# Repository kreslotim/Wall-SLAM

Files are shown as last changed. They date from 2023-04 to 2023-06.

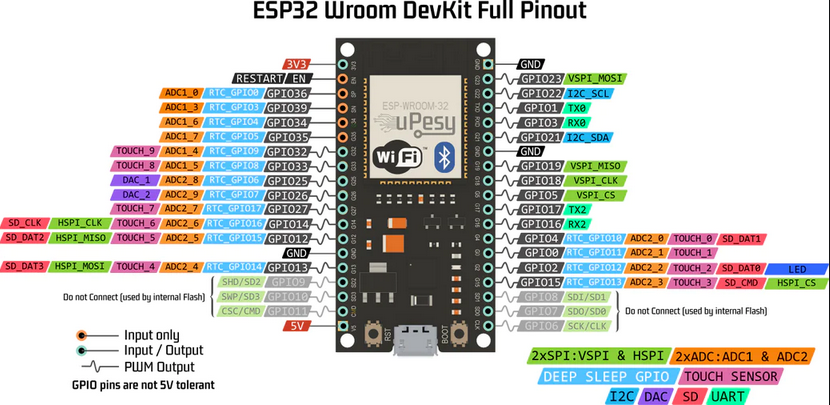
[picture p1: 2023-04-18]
circuit/ESP32-WROOM-38PINS.png

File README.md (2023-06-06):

# Wall-SLAM - Simultaneous Localization And Mapping

Timofey Kreslo, Sylvain Pichot, Finn MacNamara, Alonso Coaguila, Florian Dejean.



June 2023

## Description

Wall-SLAM is a project that we have developed within the course CS-358 Making Intelligent Things, under the direction of Prof. Koch and under the supervision of Federico Stella and Anirudhh Ramesh. This report outlines the key features, methodology, challenges faced, and a detailed “How To Build” guide.

Our [project proposal](https://github.com/kreslotim/Wall-SLAM/blob/main/proposal/proposal.md), can be useful to understand some deviations in our project from our expectations.

The primary objective of the project was to build a cost-effective and compact SLAM robot capable of mapping unknown and dynamic environments.

## Overview

https://github.com/kreslotim/Wall-SLAM/assets/56829239/a7d6daf9-7e9c-4008-a5e7-d5f0c00a2a69

Main idea:

We utilize the data from the distance sensors (Ultrasonic and LIDAR), IMU (Inertial Measurement Unit) sensor, and Stepper motors to estimate the robot's pose (position and orientation) and simultaneously construct a map of the environment. All this data will be processed and then displayed on a website. This involved integrating data from different sensors using techniques such as sensor calibration, fusion and Kalman filtering algorithms.

## Components and supplies

- ESP32
- NXP Precision 9DoF IMU
- VL53L1X Time of Flight Distance Sensor (2x)
- HC-SR04 Ultrasonic Sensor
- 180-Degree Servo
- Stepper motor 28byj-48 (2x)
- ULN2003 motor driver (2x)
- XL6009E1 DC-DC Voltage Converter - 5V
- 9V Battery supply
- Power Switch
- 3D Prints (STLs)

## 3D Design



As zealous devotees of the enchanting Disney’s figure Wall-E, we couldn’t resist the temptation to transform our prototype into his spitting image. But, alas, our professor promptly intervened, bursting our bubble of whimsy with a comic remark. He reminded us that while Wall-E excelled in garbage collection and exuded undeniable cuteness, our project’s aspirations extended beyond those realms. Thus, we bid farewell to our beloved Wall-E robot, sparing it from a destiny of cuteness overload and instead refocusing our efforts on more practical endeavors.

We decided to shift our focus to functionalities that would enable mapping of the surrounding environment, which is covered by SLAM. Additionally, we chose to retain the concept of tracks with wheels, as it offers enhanced precision in movement and rotation (especially the ability to turn on the spot), while opting for rubber tracks to minimize slippage during maneuvering. The adventure of building a SLAM robot starts here. Our first step is to build our robot, that we later named... Chewbacca, we will give a reason for that name at the end of the report. Meanwhile lets see how we built it. 

 <br/><br/>

### 1. Sketches



We started by sketching our ideas and figuring out how to arrange electronic components in the best way possible. Our main goal was to create a compact design that would make the assembly process easier and speed up 3D printing. This approach aimed to make the construction phase more efficient overall.

We initiated the development process by focusing on the chassis design. Subsequently, we proceeded to devise an arrangement strategy. The robot incorporated two stepper motors along with their corresponding drivers, a servo, a battery, and a micro-controller. For the initial prototype, we positioned both stepper motors at the rear section of the chassis. In order to counterbalance the weight distribution, the batteries and the micro-controller were placed at the front section. Lastly, the servo, responsible for holding the sensors, was centrally positioned within the chassis.



This approach was promptly dismissed as it became apparent that in order to facilitate turning, both motors needed to rotate in opposite directions, necessitating the rotation of the entire car around its vertical axis.

The rotation of the machine necessitates the alignment of the servo and the primary axis of rotation. This alignment is crucial during turning maneuvers as the distance sensors are required to scan in close proximity to the adjacent wall. By maintaining the sensors in close proximity to the central axis of rotation, the objective is to minimize noise and optimize the accuracy of the scanning process.

Consequently, we proposed an alternative design to address this limitation.

This design greatly appealed to us, and we made the decision to proceed in this particular direction. During our exploration on the web, we chanced upon a robot named [SMARS](https://www.smarsfan.com/) (Screwed/Screwless Modular assemblable Robotic System), which seemed to align closely with our envisioned requirements. We found inspiration in its design and opted to incorporate a chassis that closely resembled to SMARS. To assess the feasibility of the track concept, we even went as far as designing the entire SMARS idea to evaluate its effectiveness.

Having appreciated the remarkable ingenuity behind the notion of using the printing filament as a means to securely bind the tracks together, as well as the exceptional functionality of this approach in practical implementation, we wholeheartedly adopted this design for our project. Consequently, this decision entailed the utilization of the same wheels, as the tracks had been meticulously tailored to ensure precise compatibility with these specific wheel components. This deliberate alignment not only guaranteed optimal performance but also facilitated seamless integration between the tracks and wheels, thereby fortifying the overall effectiveness of our system.

The subsequent focus of our attention revolved around the development of the chassis, and the incorporation of the battery, the motors and the sensors.

As soon as we agreed on the placement of all the components, we started designing in 3D. In order to leverage the collaborative design features, we opted to use Fusion 360, allowing for effective teamwork during the design process. Minor design changes have been made in FreeCad, in order to save time.

Here’s what we’ve come up with.
<p align = "center">
 
 
</p>

Now we will explain the choice we’ve made for positioning the electronic pieces. The parts that are highlighted in green are those that we designed ourselves. The Ultrasonic sensor’s frame as well as the wheels and the tracks were borrowed from SMARS project, because they fit our requirements well.

<p align = "center">

</p>

While we adopted the wheel design from SMARS ([link for STLs](https://www.thingiverse.com/thing:2662828)), we had to adapt it’s axle mount to fit the rectangular axle of the motor we are using. Furthermore, it is essential to align the axle of the slave wheel with the motor’s axle to ensure that both wheels are at the same level.

<p align = "center">

</p>
 
In order to optimize the efficiency of the printing and assembly process, we strategically positioned all the components in close proximity to one another, ensuring minimal wasted space on the chassis.

As the heaviest electronic component of the entire construction, the battery serves as a central anchor within the overall design. By positioning it at the center, we establish a stable foundation upon which the remaining components, i.e. the servo and the sensors are securely mounted and connected.

<p align = "center">

</p>
 
The cover slides over the battery and encases the servo on top.

The servo, in return, holds both lidars (distance sensors) that are sneaked on the servo’s arm.
<p float = "left">


</p>
 
### 2. Assembly

Once the design was ready, it was printed at EPFL in DLL, and partly at home. Mostly PETG material was used, except for the tracks which were printed using FLEX rubber filament, under the consent of Sébastien Martinerie - 3D printing Coach at the SPOT. Caterpillars are connected by means of an ordinary filament in its initial form, as mentioned above.
<p align = "center">

</p>

To make power control easier, a switch has been added on top of the cover that holds the servo.
Given that multiple components, including the Arduino, operate at the same power level and share a common ground, the wires are soldered together in a centralized manner resembling the arrangement of an octopus




The opposite side of the switch features the motion sensor (IMU) securely attached to the cover that holds the servo, using screws:
<p align = "center">

</p>

<br/><br/>


Here the difficulty turned out to be to establish connections between numerous devices that rely on the I2C (Inter-Integrated Circuit) serial communication protocol. In particular, there was an issue with two lidars having the same address, preventing them from being connected on the same I2C bus. One possible solution would have been to use a multiplexer, but since one was not available, an alternative approach was devised through code.

<br/><br/>

To overcome this challenge, some of the ESP32 GPIOs needed to be reconfigured to function as I2C pins, to which we connected the front lidar. Subsequently, the motion sensor was connected to the standard I2C pins, and the back lidar was also connected to these same pins as well. This was possible because the motion sensor and the lidar had different addresses assigned to them, ensuring that there was no conflict in their communication over the shared I2C bus. Finally, to ensure proper insulation and protection, we applied heat shrink tubing at the junction point where the three wires met.

<br/><br/>
<br/><br/>

A detailed circuit diagram of all connections is shown below:

<p align = "center">

</p>

In conclusion, the assembly of our car involved strategically placing two lidars on top of a servo that rotated around the same vertical axle as the car itself. This configuration enabled us to detect obstacles within a proximity of 4 meters by performing a single 180-degree servo rotation. 

Additionally, we positioned an ultrasonic sensor at the front of the car, ensuring continuous forward movement while avoiding potential collisions. If an obstacle was detected directly in the car's trajectory, the sensor would halt the motors, allowing the program to recalibrate and determine an alternate path for the car to follow. These careful arrangements and sensor placements greatly enhanced the car's obstacle detection and navigation capabilities, ensuring a safer and more efficient operation.

### 3. Problems and Risks

There were several risks and issues we encountered during the project, primarily related to the management of batteries. One significant problem arose from the frequent changing of batteries, which required manipulating multiple components and wires. In hindsight, it would have been more advisable to use a LIPO battery that offers greater stability and ease of use. 

Additionally, a critical mistake was made when we placed the voltage regulator on a very thin layer of double-sided tape directly attached to the battery case, which had metal circles on its surface. This design flaw led to a potential short circuit between the six batteries and the voltage regulator when components were pushed against each other. This short circuit had the potential to cause severe damage to the entire system and possibly lead to its complete failure or even a fire hazard.

Therefore, we implemented a solution by adding a small cardboard spacer to provide insulation and maintain a safe distance between the electronic components.

Another significant issue we faced was related to the control of the steppers, which proved to be too slow for our project's requirements. While the car moved at a slow pace, the map updates occurred rapidly, causing a bottleneck in our system. Initially, we chose these specific steppers to ensure precise positioning. 

However, this decision posed challenges as the tracks on which the car operated became increasingly loose over time. Prolonged use resulted in the tracks losing their elasticity, leading to deviations from a straight line. Specifically, one side of the car moved faster than the other, exacerbating the issue of maintaining a consistent trajectory. By securing the tracks with the elastic bands, we effectively restored the required tension and stability, mitigating the issue of one side of the car moving faster than the other.

In retrospect, alternative steppers with higher speed capabilities could have been a more suitable choice to address this problem.

## Data & Algorithm Software

Unfortunately, the SLAM algorithm is too memory-bound and computationally slow for a microcontroller. To address this issue, we have the microcontroller connect via Wi-Fi to a capable external computer called the Command Computer (CC). This is why the microcontroller used has Wi-Fi capability. The Wi-Fi connection also allows the robot to move freely. Therefore, the microcontroller only receives commands movement and returns sensor data to the CC. 

**The different tools** we developed for this are:

### 1. **Web Interface**

To see in real time the advancement of the mapping and for debugging purpose, we made a complete interface that display every step of the data flow. To do so, we are using Flask, Plotly and bootstrap.


 
*Sample setup*

- *Communication frequency* : shows the number of data packages sent and received, as well as the number of obstacles detected.
- Orientation Line Chart: shows the sensor fusion of the accelerometer and magnetometer and its variation.
- *Noisy Obstacle Detection*: This is a map without any filter, displaying every data point no matter how weird it is. This allows us to clearly see how much data we filter out.
- *Redundancy Check*: This is a map that has undergone a first cleanup.
- *K-Mean Graph*: This map is a visual representation of obstacles. With some basic machine learning that we have optimized, we can map and understand the environment with greater ease. The path calculated using Dijkstra is display with the current position and the togo position.

### 2. **The Different Algorithms**

To navigate and treat the data we receive from the robot we have elaborated different algorithms to efficiently put them to use. 

- **Pathfinding Algorithm:**
    
    We used Dijkstra's algorithm which is a popular pathfinding algorithm used to find the shortest path between two nodes in a graph with non-negative edge weights. We applied more weights to nodes if there was a change in direction (due to the fact that our robot loses a lot of time during turns, and also imprecision adding up with the turns) and less to the nodes that the robot hasn’t visited yet. 
    
    To create the graph with the nodes, we run K-means on the list of filtered obstacles. We then render the node inaccessible if the cell containt an obstacle/cluster calculated by Kmean. Kmean also determines the best targeted position (more detail on that below).
    
    One challenge was to translate global instructions into instructions that the car can understand, which are limited to goForward(), turnLeft(), and turnRight(). Hence, we ran Djikstra every 0.5 seconds to find the new best move to apply to the robot depending on its current position and orientation. This solution is costly, but is robust since imagine if all of a sudden we remove an obstacles the robot sees that there is immediately a new optimal path. This hence enabled the robot to react to it’s environment.
    
    *Photo of the Pathfinding Algorithm in action right below…*
    
- **Map - kmean.py and mapK.py**
<p float = "left">


</p>

   In order to determine if there is a real obstacle, we are using kmean algorithm to determine their position and center. Finding those center are useful to move to the less dense zone, the zone that is unexplored or empty. Due to our Djikstra algorithm, we added high weight to already explore area, hence resulting in a path that will always try to explore. If a path cannot explore anymore, this mean we have map the whole area.
    
   - Kmean try to assign K cluster to a data set and optimize the distance between the point from a center.
       - To determine the best K, so our number of obstacle, we run multiple time the algorithm and look for the minimal distance of the cluster related to their center. ***(Elbow method)***
        - To initiate our center, we already approximate where the center should be ***(kmean ++).*** Then we move again the center to approach the center of mass better till we converge.
    
   - In order to reduce noise, which can be seen as the outlier and stand alone point in our dataset, we slice our data randomly before training kmean. If a cluster is assign less than a fixed number of point, we will modify the label to be considered as a noisy cluster, represented with the red dots on the above graphic.
    
   - To represent an obstacle, we decided to turn them into rectangle taking the minimum and maximum. This lead to more strict threshold since our obstacle are hollow shape and to create multiple rectangle for one obstacle depending on its size.
    
   **kmean.py** handle all the necessary function to run the kmean++ algorithm and the Elbow method using numpy.
    
   **mapk.py** handle how to interpret this data in your main app.
    
- **Noise Correction - Kalman**
    
    In order to combine our sensor, we utilize known variance of them to correct sudden noise.
    
    - Using the acceleration from the IMU, the actual speed of the robot can be determined for a short period. A better estimate can be determined with a Kalman filter by combing the IMU measurements and the speed inputted in the steppers. What the Kalman filter does is an estimate by combining our prediction of speed and the correlated measurement of acceleration through the covariance of our prediction and our measurements. The covariance was gathered from the documentation from the physical components, being the IMU and the stepper motors. Unfortunately, we could not accurately implement a Kalman filter due to multiple reasons. First of all, the stepper motors lacked proper and clear documentation regarding their covariance regarding their position and speed so this led to estimating a covariance. Second of all, we lacked experience with developing Kalman filters. Third of all, the stepper motors are too precise and the IMU is too imprecise, rendering fine tuning very difficult. Each reason exacerbated the next one. The final straw was when it was found that multiplying a scalar to the steps done by the stepper motor was more precise and requires less computation. Nevertheless, we believe that a Kalman filter is possible to implement for the simultaneous localization but given that a simpler and more efficent solution provided with better results than the prototype. If a Kalman filter were to be implemented, we would recommend replacing the stepper motors with an alternative.
    
    - We successfully utilized fusion algorithms combining the magnetometer and gyroscope of the IMU to compute a highly accurate heading orientation. Among the available filters, the Mahony filter provided the fastest results but lacked precision, while the Madgwick and NXP Sensor Fusion filters offered greater accuracy at the cost of slower computation.
        
        In our implementation, we employed the [NXP Sensor Fusion](https://github.com/adafruit/Adafruit_AHRS/blob/master/examples/calibration/NXP_FXOS_FXAS.h) algorithm, which was developed by the creators of the [Adafruit IMU](https://cdn-learn.adafruit.com/downloads/pdf/nxp-precision-9dof-breakout.pdf) we utilized. By leveraging this precise heading calculation, we implemented an autocorrection mechanism using a Kalman filter for the car's orientation. Every period of time, we checked if the orientation difference exceeded a predefined threshold, prompting us to adjust the stepper motor with a constant number of steps. 
        
        This autocorrection was necessary due to the loose tracks on which our car operated. Initially, the freshly printed rubber filament tracks performed flawlessly until they were stretched too much, reducing their elasticity and causing them to scroll in empty space. As a result, one side of the car moved slower than the other, leading to slight deviations from a straight line. 
        
        To demonstrate the effectiveness of the Kalman filter on the orientation, a graph displaying three different orientations is presented on the web interface. It is evident that the gyroscope-based orientation exhibits significant deviation, while the magnetometer-based orientation closely matches the precision achieved by the heading computed using the Kalman Filter. 
        
- **Data Validation - Redundancy**
    
    In order to check if a data point was even ready to be considered an obstacle in the real life, we perform a redundancy check. A simple check if the obstacle is still present or a check to see if there is enought detection points for it to be considered as an actual obstacles before giving the the list of points to as an input for K-means 
    
    *Here is a the graph without the filter:*  
    noisy_example

    *Here it is with the filter (the lump present in [0,200] is the charging cable attached to the car with is accidental and not present in the photo with the observed obstacles):*
    filter_example

### 3. **TCP Connection ESP32 ↔ CC (Python)**

In order to process our data, we utilize a python code that run intensive computation and take avoid the heavy computation from the ESP32. To do that we need to have great connectivity between the two : esp32.py and espComm.ino are the two files responsible of communication.

- *EspComm.ino*  : Sets up a WIFI access point to allow the CC to connect. It opens two ports, a sending port and a receiving port. This prevents us from mixing the data up. The code sets up an Access Point using the ESP32's built-in WiFi capabilities. It creates a server to receive data on one port and send data on another port.
    
    ```arduino
    //Open Wifi Port
    WiFiServer sendServer(SEND_DATA_PORT);
    WiFiServer recieveServer(RECIEVE_DATA_PORT);
    
    //Open WifiClients
    WiFiClient sendClient;
    WiFiClient recieveClient;
    
    // Configure IP addresses of the local access point
    IPAddress local_IP(192, 168, 1, 22);
    IPAddress user_IP(192, 168, 1, 23);
    
    IPAddress gateway(192, 168, 1, 5);
    IPAddress subnet(255, 255, 255, 0);
    
    void setup() {
      // Access Point SetUp
      WiFi.softAPConfig(local_IP, gateway, subnet);
      WiFi.softAP(ssid, password);
    
      // WifiServer Setup
      sendServer.begin();
      recieveServer.begin();
    	...
    ```
    
    The interesting part about the Arduino connection is the problem we had with running the motors simultaneously with the data connection. The Arduino data transfer needed some time to run, on the other hand the stepper motors needed instructions as fast as possible due to the fact that we were stepping them step by step (check the AccelStepper.h library for more: [https://www.airspayce.com/mikem/arduino/AccelStepper/classAccelStepper.html](https://www.airspayce.com/mikem/arduino/AccelStepper/classAccelStepper.html)). The two pieces of code couldn’t run on the same core so we utilize the Arduino’s second code 
    
    ```arduino
    void setup(){
    	...
    	// Setup core to Move
      xTaskCreatePinnedToCore(
        Task1code, /* Task function. */
        "Task1",   /* name of task. */
        10000,     /* Stack size of task */
        NULL,      /* parameter of the task */
        1,         /* priority of the task */
        &Task1,    /* Task handle to keep track of created task */
        1);        /* pin task to core 0 */
      ...
    }
    
    void Task1code(void* pvParameters) {
      for (;;) {
        action(actionNumber);
      }
    }
    
    void loop() {
      if(WiFi.softAPgetStationNum() == 1){
        sendData();
        readData();
        delay(10);
      } 
    }
    ```
    
    Fun fact ‘loop()’ is running by default on core 0. Here with this setup Task1Code is running on core 1. Here is a link for more information about how to set up an ESP32 with two cores : [https://randomnerdtutorials.com/esp32-dual-core-arduino-ide/](https://randomnerdtutorials.com/esp32-dual-core-arduino-ide/)
    
    We quickly dove in other methods of connection :
    
    - We tried having our the ESP32 connect throug our access point created by our laptop, but our amazing firewall prevented us from using the ports directly. To prevent any security issue we decided not to play around with it. 
    
    - We tried Bluetooth connection as well. Unfortunately even if we were able to successfully create the link with the computer the fact that we only had one port we got a lot of data confused. So we decided to stick with the ESP32 just creating an access point.
    
- *Esp32.py* : This automatically connect to the WIFI generated by the EspComm.ino.
    
    ```python
    import pywifi
    def connect_to_wifi(self):
            iface = wifi.interfaces()[0]  # Get the first available network interface
    
            iface.disconnect()  # Disconnect from any existing Wi-Fi connection
            time.sleep(1)
    
            profile = pywifi.Profile()  # Create a new Wi-Fi profile
            profile.ssid = self.ssid   # Set the SSID (Wi-Fi network name)
            profile.auth = pywifi.const.AUTH_ALG_OPEN  # Set the authentication algorithm
    
            # Set the encryption type and password
            profile.akm.append(pywifi.const.AKM_TYPE_WPA2PSK)
            profile.cipher = pywifi.const.CIPHER_TYPE_CCMP
            profile.key = self.password
    
            iface.remove_all_network_profiles()  # Remove all existing profiles
            temp_profile = iface.add_network_profile(profile)  # Add the new profile
    
            iface.connect(temp_profile)  # Connect to the network
            time.sleep(5)
    
            return iface.status() == pywifi.const.IFACE_CONNECTED # if the connection is sucessfull or not
    ```
    
    Once connected we will listen for any socket communication and if the Esp sent a message we will be able to get it’s IP. 
    
    ```python
    while self.espIP is None:
                try:
                    self.get_info= socket.socket()
                    self.get_info.setsockopt(socket.SOL_SOCKET, socket.SO_REUSEADDR, 1)
                    self.get_info.bind(('0.0.0.0', self.recv_port))  # bind to a local address and port
                    self.get_info.settimeout(3.0)  # set a timeout of 3 seconds
                    self.get_info.listen(0)  # start listening for incoming connections
                    self.recv_socket, client_address = self.get_info.accept() # Wait to receive a transmission
                    self.get_info.close() # Close the socket 
                    self.espIP = client_address[0] # From the answer, get the IP assign to this device
                except Exception as e:
                    print(f"No information was sent by ESP, retrying... {e}")
    ```
    
    Next we will create another socket to be able to send command to the Esp too
    
    ```python
    self.send_socket = socket.socket(socket.AF_INET, socket.SOCK_STREAM)
    self.send_socket.settimeout(5)  # set a timeout of 2 seconds
    self.send_socket.connect((self.espIP, self.send_port))
    ```
    Then to read or sent data, we can simple run those command. We will pin a thread to constantly run __listen().

    ```python
    def __listen(self):
            while self.running:
                if self.connected:
                    try:
                        # Receive data from the client socket
                        data = self.recv_socket.recv(48)
                        if data:         
                            data_decoded = struct.unpack('ffffffffffff', data)
                            # Use the data 
    	                        ....
    
                    except Exception as e:
                             print("Connection error :", e)
    												 self.connected = False
    ```
    
    Here, this code is responsible for sending an action number over a socket and waiting for a response from an ESP32 device. It handles connection errors and provides success/failure status codes.
    
    ```python
    def __send_actionNumber(self, actionNumber):
            if self.connected:
                try:
                    # Send the packed angles over the socket
                    data = struct.pack('f', actionNumber)
                    self.send_socket.sendall(data)      
                    response = 0
    
                    while (not response == "200") :            
                        response = self.send_socket.recv(1024).decode()   
                        print("Received response from ESP32:", response)
    
                except Exception as e:
                    print("Connection error :", e)
                    self.connected =False
                    return 400   # Connection failed   
                return response # Sucess, will output code 200
            return 400 # Connection failed
    ```
    
    In case of failure, a thread will be tasked to restart the connection procedure and turn the boolean self.connected to true again.
    
    Below you can find the UML diagram that we designed and used as a reference to coding our classes:

### Problems and Risks

One of the main issues we ran into, is the instability of the connection. In early stage of the project, we had to manually connected to Wifi, due to frequent reboot of the esp, our OS refused to directly reconnect leading to wait a few minute for between every try. The solution we found was to force the reconnection by using a python library.

### 4. Simulation

At an earlier stage of the project, we tried to create a simulation to test different algorithms but unfortunately we had to divert our attention to other aspects. Nevertheless a prototype was developed, in which the robot is represented as a point mass and the landmarks are a string of 2d points.

To simulate the LIDAR that the robot used, we created a python class with static methods to handle the light collisions with Numpy with the shapes called Geometry which was called by the Playground class which would contain all the landmarks which was called by the Rover class which represents the robot. To get a better picture of the area, the rover could move from point to point. To add some realism, every time rover scanned it would add a noise random varialbe that is ajustable with a modifiable scalar.

simulation

As mentioned before, we ended up not using the simulation much, with hindsight, we admit that it was not useful within the time frame we had. Maybe if the time frame was bigger, we could have used it to develop the the navigation algorithmns, it could have helped with not having to depend on the robot for more realistic tests and allow parrallel workflows.

### 5. Software Overview

software_overview

### 6. Problems and Risks

Due to how little testing we were able to do in real scenarios, our kmean hyperparameters may not fit for a complete mapping or may need to be adjusted depending of the size explored.

## Why Chewbacca ?
We decided to name our robot Chewbacca, with all his wiring they just look similar. Chewbacca has problem navigating around his surrounding with all of hair covering his eye just like our robot. Chewbacca has his powerful blaster, our robot has powerful Lidar guns. Chewbacca has two legs, our robots has two motors. Chewbacca has good balaance, our robot has an IMU that can easily find his orientation. We hope you enjoyed the little adventure with our Chewbacca, sadly this is the end of his story... or is it ?   
<p align = "center">

</p>

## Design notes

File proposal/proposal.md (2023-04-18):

# CS-358 Making Intelligent Things
## Project : Wall-SLAM - Simultaneous Localization And Mapping
Timofey Kreslo, Sylvain Pichot, Finn Mac Namara, Alonso Coaguila, Florian Dejean

March 2023

## Contents
    • 0.1 Description and motivation of the project  . . . . . . . . . . . . . . . . . . . . . . 1
    • 0.2 How are we going to build it ? . . . . . . . . . . . . . . . . . . . . . . . . . . . . 2
    • 0.3 Resources  . . . . . . . . . . . . . . . . . . . . . . . . . . . . . . . . . . . . . . 3
    • 0.4 Risks  . . . . . . . . . . . . . . . . . . . . . . . . . . . . . . . . . . . . . . . . 3
    • 0.5 Buy list . . . . . . . . . . . . . . . . . . . . . . . . . . . . . . . . . . . . . . . 5
    • 0.6 Milestones . . . . . . . . . . . . . . . . . . . . . . . . . . . . . . . . . . . . . . 6
    • 0.7 Weekly Tasks . . . . . . . . . . . . . . . . . . . . . . . . . . . . . . . . . . . . . 7
    • 0.8 Progress documentation . . . . . . . . . . . . . . . . . . . . . . . . . . . . . . . . 8
    • 0.9 References . . . . . . . . . . . . . . . . . . . . . . . . . . . . . . . . . . . . . . 10

## 0.1 Description and motivation of the project
Our project involves building a robot that will perform Simultaneous Localization and Mapping
(SLAM). SLAM is a crucial technology for robotic systems that need to move in dynamic and
unknown environments. Robots equipped with SLAM can map and navigate their surroundings
without human intervention, making them valuable for various applications such as warehouse
automation, search and rescue operations, etc... In general, the sensors used on SLAM robot are
quite expensive and big so our objective would also be to reduce the size and price.

We will utilize an ultrasonic sensors system (see following section for the sensor discussion)
to implement the SLAM algorithm, and we will develop a software program that will render the
robot autonomous via Wi-Fi. This will require integrating various components of the robot, such
as the motor control system, the ultrasonic sensor system, and the Wi-Fi communication module.

Overall, the project consists of deploying an autonomous robot that will map its surrounding
area using SLAM algorithm with an end goal of displaying a cohesive 2D-map of the area.



## 0.2 How are we going to build it ?
### Obstacle detection
Lidar and ultrasound are both commonly used sensors for Simultaneous Localization and Map-
ping applications. However, Lidar has the following advantages:

   - 1. **Accuracy**: Lidar sensors provide much higher accuracy measurements than ultrasound.
    Lidar can measure distances with a precision of a few millimeters, whereas ultrasound can
    only measure distances to within a few centimeters. Also the resolution is much higher.
   - 2. **Noise immunity**: Lidar sensors are less susceptible to noise and interference than ultra-sound sensors. Lidar uses light to measure distances, whereas ultrasound uses sound waves.
    This makes Lidar less sensitive to acoustic noise and interference.
   - 3. **Mechanical aspect**: Lidar has a bigger range or aperture angle (in degrees) so i would
    need to be spun around, unlike the ultra sound solution.
    
Overall, Lidar sensors provide much more accurate and detailed information about the envi-
ronment, which is essential for accurate SLAM. The problem with Lidar is that it is expensive
and has the potential to blow the budget.

Consequently, we will opt for an ultrasonic sensor which is a cheaper alternative of a Lidar
sensor. The sensor gives us the distance D with the detected obstacle. Two ultrasonic sensors
will be rotating on top of the robot (back-to-back on a 180 degrees servo, so we can plot any
obstacle around the robot) (ex: https://howtomechatronics.com/projects/arduino-rad
ar-project/). Software wise : Knowing the direction of the ultrasonic sensor we can create a
block (representing an obstacle) of a distance D from the sensor).


 


### Robot localization
To determine where the robot is on the map we will use two stepper motors, the inputs given to the motors allow us to calculate the position of the robot based on its starting point.
(https://www.youtube.com/watch?v=5CmjB4WF5XA). 
Regarding the software, we need to create an algorithm that creates a link between the current position and the new targeted position without going through obstacle. To limit inaccuracy, we will use an IMU to determine the orientation of the robot (ex: https://www.youtube.com/watch?v=KMhbV1p3MWk).

### Computational Work
Unfortunately, the SLAM algorithm is too memory bound and computationally slow for a micro-
controller. To deal with this problem, we plan having the micro-controller connect through Wi-Fi
to a capable external computer, the Command Computer (CC), hence why the micro-controller
used has Wi-Fi capability. The Wi-Fi connection also allows the robot to move freely. Therefore,
the micro-controller only receives commands for movement and returns the sensors data to the
CC.

### Algorithm & Data
To create the map and control the robot with the CC, the micro-controller will collect and send
to the CC the following elements: the position of the robot, the orientation of the robot (IMU),
the distance detected from the ultrasonic sensor and the orientation of the sensor (180 Servo).
Then using the data it receives, the CC generates the map and sends new commands to the robot
from a distance. We want to use Python and the Robot Operation System (ROS) as a framework
since its industry standard and can provide a myriad of useful tools/resources. Regarding ROS
and Arduino compatibility, we have found the following solution. If we have time, we might use
some basic machine learning algorithms to detect noise.

## 0.3 Resources
Firstly, we have discovered open-source projects and tutorials available at :
- https://wired.chillibasket.com/3d-printed-wall-e/
- https://3delworld.com/how-to-make-smars-robot-3d-printed-2023/
- https://youtu.be/htoBvSq8jLA (position tracking)

That gives us access to numerous STL files for SMARS parts. These files include components
that we can use to construct our SMARS robots for SLAM. This will save us a significant amount
of time and effort, as we do not need to design and model these parts from scratch.

Additionally, we have also developed a program, last year, for efficient route finding using
Dijkstra algorithms. This program will be instrumental in enabling our robot to navigate through
the environment autonomously while avoiding obstacles. The Dijkstra algorithm is a graph-
based algorithm that finds the shortest path between two points in a graph. We will modify this
algorithm to suit the needs of our project, such as incorporating the sensor data from the camera
vision system to avoid obstacles in real-time.

## 0.4 Risks
1. **Mechanical issues**:
We are using precise steppers motors, to navigate through the map but we still need to take
into account error accumulation. This can be an issue since we are planning continuously
updating the robots position via the stepping information of the motors.
Also using tracks could turn out to be a bad idea, because tracks slip when touring on the
spot, resulting in screwed up data for odometry (=”use of data from motion sensors to
estimate change in position over time”).

Solution: We added an IMU sensor to check the rotational information. In case this does
not work, we need to consider a simplified design of the chassis, a bit like an automatic
hoover. (That is, only two wheels and one stabilizing thing in front/back).
After all, there is a reason why those vacuum cleaners are built the way they are.
Now, if it still has problems on the localizing part, we need modifying the area. to map
and setting up some kind of orientation system (reflective tape around cylinders is common
way in industrial environments, an easier way would be to simply add a grid like pattern
for the robot to follow on the ground).

2. **Sensor accuracy**:
Our SLAM robot rely heavily on ultrasonic sensors to navigate and build maps of their
environment. These sensors must be accurate and reliable, otherwise the robot will struggle
to locate itself or map its surroundings. The sensors should be as good as possible.

Solution: If the ultrasonic sensors are inaccurate, means that we would have to change the
placement of the sensors, worst case scenario the sensor has to be right in front of the wall,
we would put the sensor in front of the car and make it work similar to a Roomba.

3. **Environmental Interference**:
The surface on which the robot is must be flat and stable, if those condition aren’t respected
we will easily lost the position of the robot, making it challenging for the robot to navigate
and detect its surroundings accurately, resulting in a poor map.

Solution: We will restrain the robot environment to avoid that, and in case of such en-
vironment we will able to detect them due the gyro (IMU) and stop the algorithm if the
environment is unavoidable. An example of such will be a small jump that if the robot is
not aware of it, it will get flipped.

4. **Computational power**:
Building a SLAM robot requires significant computational power to process sensor data,
run algorithms, and control the robot’s movements. The ESP8266 lacks this power.

Solution: Computation will be done on a laptop with wireless communication.

5. **Communication problems**:
Our SLAM robot will rely on wireless communication to receive commands or send data,
and any communication problems can lead to delays or malfunctions in its real time map-
ping ability.

Solution: We could try Bluetooth instead but the problem might still arise. We can use
a cable but that strongly reduces the mobility of the robot. Another approach will be to
await till good communication is made, every time there seem to be a perturbation.

## 0.5 Buy list
SMARS robot (total 120.- frs):
### Electronics 1x SMARS
    1. ESP-32                                                     1x (14.-)
    2. Stepper Motor / (replaced by smaller motor 5V)             2x (22.-)
    3. A4988 Motor Driver                                         2x (3,9)
    4. Ultrasonic Module Distance Sensor HC-SR04                  2x (4,5)
    5. Battery Block Coupler 6 Battery 9V [Same as the lego car]  1x (5.-)
    6. 9 axis ICM-20948 9DoF IMU                                  1x (24.-)
    7. 180 Servo Motor                                            1x (2 for 15.30.-)

We wish to build a second SMARS for optional goal and to have some redundancy in case one
part fails. 
SMARS robot illustration:



## 0.6 Milestones
### • Milestone 1 : Build a 3D PRINTED prototype of the chassis with working step-per motors, check track driving behaviour and get communication between the computer and the vehicle+sensors to work (Deadline : 1st May).
(From Week 6 - 7)
* Task 1: Design and print the chassis prototype for our vehicle.
* Task 2: Assemble and collect all the necessary hardware and sensors. So we can rapidly combine it with the 3D parts
* Task 3: (Start coding the software) Find a way to collect the data from the sensors/Arduino and send them to the CC via Wi-fi.

FIRST SMARS PROTOTYPE should be built on the 7th of April

(From Week 8 - 9)
* Task 4: Check that the sensors work well and that the output are correct. So we can change the sensors if we aren’t satisfied with the current ones
* Task 5: Transfer the output of the robot on a map, so we can start utilizing the data.
* Task 6: Create an algorithm that moves the car from an initial position to another given position. Starting to send instruction to the SMARS from the CC to see if are able to correctly control the robot.

### • Milestone 2: Implement an algorithm that allows the robot to create a map of its environment and return to its initial position using the map.(Deadline : 26th May)
(From Week 10-11)
* Task 1: Code the mapping and localization algorithm, needs to be autonomous. So we can start plotting the obstacles.
* Task 2: Test the limit of our robot and debug the mapping and localization algorithm, if any problem are detected.

OVERALL WORKING SLAM ROBOT should be able to map on the 20th of May

(From Week 11-13)
* Task 3: Have a working SLAM robot.
* Task 4: Have a working UI.

### • Optional Goal: Scale up the number of SMARS
The integration of another robot. The goal would be to reduce the time needed to map out
an area. One of the possible solution would be by scaling up the number of robots working
together. This is might be quite complicated, and we haven’t really thought of it yet but
we are leaving the door open.
### • Optional Goal: Sound integration
It would be amazing if the robot could produce noises/music on command, or produce noises in real time through Wi-Fi. This would allow the robot to communicate in real time to a person blocking its way or allowing it to call for help if it is stuck.

## 0.7 Weekly Tasks
This section is to split up the jobs, that have to be done, evenly with the team members. We
plan weekly team meetings between us (without the Phd student) to keep us up to date on
what is going on and where we are exactly in the project. We find it important to have good
communication especially when it comes to asking for help. We will be focusing a lot on talking
and understanding the other team members. With that said the tasks here will not always be
done by the person mentioned because on the moment problems might arise or even the initial
plan wasn’t a good solution to the problem. On the other hand, we can guarantee that all team
members will have a saying in the more general tasks in the Week n°# column

    Week n°#                Tim                 Florian             Finn                Alonso              Sylvain
    6. Discussion on        Building a pro-     Modelling on        Modelling on        Modelling on        Modelling and
      how we are go-        totype version      Fusion 360,         Fusion 360 and      Fusion360,          brainstorming
      ing to design the     of the SMARS        first model         brainstorming.      second model        on the software
      robot.                (with smaller       with diagonal                           with side by        a connectivity
                            components that     stepped motors.                         side stepped        through Wi-Fi.
                            Tim has).                                                   motors.
    
    7. Analysing            Analyse 3D          Compare and         Learn how           Compare and         Draw an electric
    SMARS prototype and     printed models,     analyse 3D          to control a        analyse 3D          circuit to see if
    3D printed prototype    and draw an         printed models.     stepper motor.      printed models.     all connections 
    chassis as well as      electric circuit.                                                               are good.
    clarifying the
    electric wiring.
    
    Holidays                Do research         Do research on      Advance on          Advance on          Do research on
    Start the software      on ultrasonic       stepper motor       the circuit         the circuit         IMU and how to
    research, to learn      sensor and how      and how to          and review          and review          use it, and see
    how to correctly        to use it and       use it and see      prototype with      prototype with      how we can use
    use our equipment       see how we can      how we can          the constraints     the constraints     python to utilize
    and starting to         use python to       use python to       of the wiring,      of the wiring,      it’s data.
    understand how          utilize it’s data.  utilize it’s data.  if done check       if done check
    we are going to                                                 how to create       how to create
    design and code                                                 a 2D map with       a 2D map with
    the software.                                                   Python.             Python.
                                    
    8. Assemble the         Debugging           Playing around      Debugging           Soldering and       Soldering and
    hardware, and           the ultrasonic      with the stepper    the ultrasonic      assembling the      assembling the
    the software.           sensors code        motors and see      sensors code        hardware.           hardware.
                            and real life       how precious        and see how
                            testing.            they are            it would work
                                                code to             with the 360
                                                real life ratio).   servo.
                                                
    9. This should          Debugging.          Debugging           Debugging           Debugging           Debugging
    just be a                                   cable management    hardware if         remodelling         remodelling
    debugging week                              if necessary.       cables fall off.    if necessary.       if necessary.
    and time to reflect
    a bit on how we
    are working as a
    team.

For now, we only planned individual tasks till week 9 (for Milestone) to see the dynamic of
our group. When the first milestone is achieved, we will plan new weekly tasks for the next
milestone.

## 0.8 Progress documentation
In development from Week 7 onwards...

We started to develop the chassis for the robot. First we need consider what it needs to hold,
followed by how to arrange it. The robot will hold the 2 stepper motors, a servo, a battery and
a micro-controller. For a first prototype, the stepper motors both go in the back, to compensate
for the back weight, we would put the batteries and micro-controller in the front, finally in the
center the servo holding the sensors.



Our second prototype has the stepper motors diagonally split from each other. This version
is more campact (smaller in terms of width). 
We want to test different configurations in turns
of weight dispersion:



Here is first SMARS prototype with our own equipment. This will allow us to quickly test if
tracks are a good use in our project, so we can change our design if this isn’t the case.




## 0.9 References
* [1] Figure 1 : Alain Godot. Algorithmes SLAM (Simultaneous Localization and Mapping). May 2019. URL: https://www.innowtech.com/2019/05/16/les-algorithmes-slam-simultaneous-localization-and-mapping/
* [2] Figure 2 : @CodersCafeTech. DIY Radar With Ultrasonic Sensor And Chat-GPT Generated Arduino Code — Coders Cafe. Youtube. 2023. URL: https://youtube.com/shorts
/o7DMHJKhpws?feature=share
* [3] Figure 3 : Channel Everything. Two ultrasonic sensors on a servo for angle and distance data. Youtube. 2016. URL: https://www.youtube.com/watch?v=dHZB0WhLl8g&t=12s
* [4] Figure 4 : Hani’s Experiments. How to make an ultrasonic Radar. Youtube. 2021. URL: https://www.youtube.com/watch?v=xngpwyQKnRw
* [5] Figure 5 : Kevin McAleer. SMARS Fan. 2018. URL: https://www.smarsfan.com

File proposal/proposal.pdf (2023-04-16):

# CS-358 Making Intelligent Things Project : Simultaneous Localization And Mapping

Timofey Kreslo, Sylvain Pichot, Finn Mac Namara, Alonso Coaguila, Florian Dejean

March 2023

# Contents

## 0.1 Description and motivation of the project

Our project involves building a robot that will perform Simultaneous Localization and Mapping (SLAM). SLAM is a crucial technology for robotic systems that need to move in dynamic and unknown environments. Robots equipped with SLAM can map and navigate their surroundings without human intervention, making them valuable for various applications such as warehouse automation, search and rescue operations, etc... In general, the sensors used on SLAM robot are quite expensive and big so our objective would also be to reduce the size and price.

We will utilize an ultrasonic sensors system (see following section for the sensor discussion) to implement the SLAM algorithm, and we will develop a software program that will render the robot autonomous via Wi-Fi. This will require integrating various components of the robot, such as the motor control system, the ultrasonic sensor system, and the Wi-Fi communication module.

Overall, the project consists of deploying an autonomous robot that will map its surrounding area using SLAM algorithm with an end goal of displaying a cohesive 2D-map of the area.

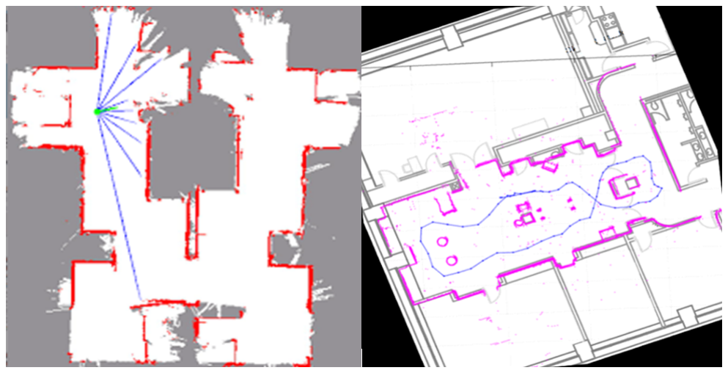
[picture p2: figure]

Source : Figure 1 (https://www.innowtech.com/2019/05/16/les-algorithmes-slam-simultaneous-localization-and-mapping/)

1

## 0.2 How are we going to build it ?

Obstacle detection
Lidar and ultrasound are both commonly used sensors for Simultaneous Localization and Mapping applications. However, Lidar has the following advantages:
1. Accuracy: Lidar sensors provide much higher accuracy measurements than ultrasound. Lidar can measure distances with a precision of a few millimeters, whereas ultrasound can only measure distances to within a few centimeters. Also the resolution is much higher.
2. Noise immunity: Lidar sensors are less susceptible to noise and interference than ultrasound sensors. Lidar uses light to measure distances, whereas ultrasound uses sound waves. This makes Lidar less sensitive to acoustic noise and interference.
3. Mechanical aspect: Lidar has a bigger range or aperture angle (in degrees) so i would need to be spun around, unlike the ultra sound solution.

Overall, Lidar sensors provide much more accurate and detailed information about the environment, which is essential for accurate SLAM. The problem with Lidar is that it is expensive and has the potential to blow the budget.
Consequently, we will opt for an ultrasonic sensor which is a cheaper alternative of a Lidar sensor. The sensor gives us the distance D with the detected obstacle. Two ultrasonic sensors will be rotating on top of the robot (back-to-back on a 180 degrees servo, so we can plot any obstacle around the robot) (ex: https://howtomechatronics.com/projects/arduino-radar-project/). (https://howtomechatronics.com/projects/arduino-radar-project/) Software wise : Knowing the direction of the ultrasonic sensor we can create a block (representing an obstacle) of a distance D from the sensor).

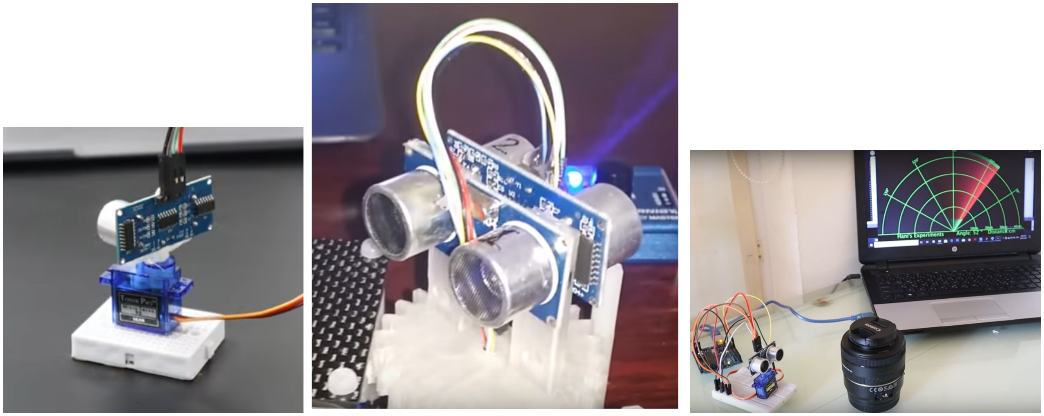
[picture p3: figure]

Source : Figure 2 (https://youtube.com/shorts/o7DMHJKhpws?feature=share) | Source : Figure 3 (https://www.youtube.com/watch?v=dHZB0WhLl8g&t=12s) | Source : Figure 4 (https://www.youtube.com/watch?v=xngpwyQKnRw)

Robot localization
To determine where the robot is on the map we will use two stepper motors, the inputs given to the motors allow us to calculate the position of the robot based on its starting point. (https://www.youtube.com/watch?v=5CmjB4WF5XA) . Regarding the software, we need to create an algorithm that creates a link between the current position and the new targeted position without going through obstacle. To limit inaccuracy, we will use an IMU to determine the

2

orientation of the robot (ex: https://www.youtube.com/watch?v=KMhbV1p3MWk).

Computational Work
Unfortunately, the SLAM algorithm is too memory bound and computationally slow for a micro-controller. To deal with this problem, we plan having the micro-controller connect through Wi-Fi to a capable external computer, the Command Computer (CC), hence why the micro-controller used has Wi-Fi capability. The Wi-Fi connection also allows the robot to move freely. Therefore, the micro-controller only receives commands for movement and returns the sensors data to the CC.

Algorithm & Data
To create the map and control the robot with the CC, the micro-controller will collect and send to the CC the following elements: the position of the robot, the orientation of the robot (IMU), the distance detected from the ultrasonic sensor and the orientation of the sensor (180 Servo). Then using the data it receives, the CC generates the map and sends new commands to the robot from a distance. We want to use Python and the Robot Operation System (ROS) as a framework since its industry standard and can provide a myriad of useful tools/resources. Regarding ROS and Arduino compatibility, we have found the following solution. (http://wiki.ros.org/rosserial_arduino/Tutorials/Arduino%20IDE%20Setup) If we have time, we might use some basic machine learning algorithms to detect noise.

## 0.3 Resources

Firstly, we have discovered open-source projects and tutorials available at :
- https://wired.chillibasket.com/3d-printed-wall-e/
- https://3delworld.com/how-to-make-smars-robot-3d-printed-2023/
- https://youtu.be/htoBvSq8jLA (position tracking)

That gives us access to numerous STL files for SMARS parts. These files include components that we can use to construct our SMARS robots for SLAM. This will save us a significant amount of time and effort, as we do not need to design and model these parts from scratch.

Additionally, we have also developed a program, last year, for efficient route finding using Dijkstra algorithms. This program will be instrumental in enabling our robot to navigate through the environment autonomously while avoiding obstacles. The Dijkstra algorithm is a graphbased algorithm that finds the shortest path between two points in a graph. We will modify this algorithm to suit the needs of our project, such as incorporating the sensor data from the camera vision system to avoid obstacles in real-time.

## 0.4 Risks

1. Mechanical issues:
We are using precise steppers motors, to navigate through the map but we still need to take into account error accumulation. This can be an issue since we are planning continuously updating the robots position via the stepping information of the motors.
Also using tracks could turn out to be a bad idea, because tracks slip when touring on the spot, resulting in screwed up data for odometry (=”use of data from motion sensors to estimate change in position over time”).

3

Solution: We added an IMU sensor to check the rotational information. In case this does not work, we need to consider a simplified design of the chassis, a bit like an automatic hoover. (That is, only two wheels and one stabilizing thing in front/back).
After all, there is a reason why those vacuum cleaners are built the way they are.
Now, if it still has problems on the localizing part, we need modifying the area. to map and setting up some kind of orientation system (reflective tape around cylinders is common way in industrial environments, an easier way would be to simply add a grid like pattern for the robot to follow on the ground).
2. Sensor accuracy:
Our SLAM robot rely heavily on ultrasonic sensors to navigate and build maps of their environment. These sensors must be accurate and reliable, otherwise the robot will struggle to locate itself or map its surroundings. The sensors should be as good as possible.

Solution: If the ultrasonic sensors are inaccurate, means that we would have to change the placement of the sensors, worst case scenario the sensor has to be right in front of the wall, we would put the sensor in front of the car and make it work similar to a Roomba.

3. Environmental Interference:
The surface on which the robot is must be flat and stable, if those condition aren’t respected we will easily lost the position of the robot, making it challenging for the robot to navigate and detect its surroundings accurately, resulting in a poor map.

Solution: We will restrain the robot environment to avoid that, and in case of such environment we will able to detect them due the gyro (IMU) and stop the algorithm if the environment is unavoidable. An example of such will be a small jump that if the robot is not aware of it, it will get flipped.

4. Computational power:
Building a SLAM robot requires significant computational power to process sensor data, run algorithms, and control the robot’s movements. The ESP8266 lacks this power.

Solution: Computation will be done on a laptop with wireless communication.

5. Communication problems:
Our SLAM robot will rely on wireless communication to receive commands or send data, and any communication problems can lead to delays or malfunctions in its real time mapping ability.

Solution: We could try Bluetooth instead but the problem might still arise. We can use a cable but that strongly reduces the mobility of the robot. Another approach will be to await till good communication is made, every time there seem to be a perturbation.

4

## 0.5 Buy list

SMARS robot (total 120.- frs):

Electronics 1x SMARS

| Name | Quantity (Price/item)
1 | ESP-32 | 1 (14.-)
2 | Stepper Motor / (replaced by smaller motor 5V) (https://www.bastelgarage.ch/stepper-motor-schrittmotor-5v-1-64-28byj-48) | 2 (22.-)
3 | A4988 Motor Driver (https://www.bastelgarage.ch/a4988-schrittmotor-treiber-stepper-driver-modul?search=a4988) | 2 (3,9)
4 | Ultrasonic Module Distance Sensor HC-SR04 (https://www.distrelec.ch/fr/capteur-de-distance-ultrasons-hc-sr04-sparkfun-electronics-sen-15569/p/30160395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) | 2 (4,5)
5 | Battery Block Coupler 6 Battery 9V [Same as the lego car] (https://www.bastelgarage.ch/batteriefach-batteriehalter-6-x-aa-mit-9v-stecker-anschluss?search=batteriehalter) | 1 (5.-)
6 | 9 axis ICM-20948 9DoF IMU (https://www.distrelec.ch/fr/capteur-de-mouvement-breakout-icm-20948-9dof-imu-sparkfun-electronics-sen-15335/p/30157561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) | 1 (24.-)
7 | 180 Servo Motor (https://www.distrelec.ch/fr/kit-de-servomoteur-180-m5stack-a076/p/30285940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) | 1 (2 for 15.30.-)

We wish to build a second SMARS for optional goal and to have some redundancy in case one part fails. SMARS robot Illustration:

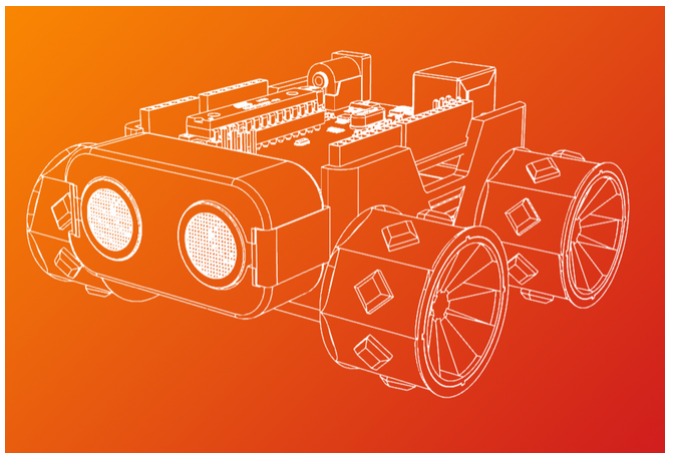
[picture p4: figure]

Source : Figure 5 (https://www.smarsfan.com/)

5

## 0.6 Milestones

- Milestone 1 : Build a 3D PRINTED prototype of the chassis with working stepper motors, check track driving behaviour and get communication between the computer and the vehicle+sensors to work (Deadline : 1st May).

(From Week 6 - 7)
Task 1: Design and print the chassis prototype for our vehicle.
Task 2: Assemble and collect all the necessary hardware and sensors. So we can rapidly combine it with the 3D parts
Task 3: (Start coding the software) Find a way to collect the data from the sensors/Arduino and send them to the CC via Wi-fi.

FIRST SMARS PROTOTYPE should be built on the 7th of April

(From Week 8 - 9)
Task 4: Check that the sensors work well and that the output are correct. So we can change the sensors if we aren’t satisfied with the current ones
Task 5: Transfer the output of the robot on a map, so we can start utilizing the data. Task 6: Create an algorithm that moves the car from an initial position to another given position. Starting to send instruction to the SMARS from the CC to see if are able to correctly control the robot.
- Milestone 2: Implement an algorithm that allows the robot to create a map of its environment and return to its initial position using the map.(Deadline : 26th May)

(From Week 10-11)
Task 1: Code the mapping and localization algorithm, needs to be autonomous. So we can start plotting the obstacles.
Task 2: Test the limit of our robot and debug the mapping and localization algorithm, if any problem are detected.

OVERALL WORKING SLAM ROBOT should be able to map on the 20th of May

(From Week 11-13)
Task 3: Have a working SLAM robot.
Task 4: Have a working UI.
- Optional Goal: Scale up the number of SMARS
The integration of another robot. The goal would be to reduce the time needed to map out an area. One of the possible solution would be by scaling up the number of robots working together. This is might be quite complicated, and we haven’t really thought of it yet but we are leaving the door open.
- Optional Goal: Sound integration
It would be amazing if the robot could produce noises/music on command, or produce

6

noises in real time through Wi-Fi. This would allow the robot to communicate in real time to a person blocking its way or allowing it to call for help if it is stuck.

## 0.7 Weekly Tasks

This section is to split up the jobs, that have to be done, evenly with the team members. We plan weekly team meetings between us (without the Phd student) to keep us up to date on what is going on and where we are exactly in the project. We find it important to have good communication especially when it comes to asking for help. We will be focusing a lot on talking and understanding the other team members. With that said the tasks here will not always be done by the person mentioned because on the moment problems might arise or even the initial plan wasn’t a good solution to the problem. On the other hand, we can guarantee that all team members will have a saying in the more general tasks in the Week n°# column

Week n°# | Tim | Florian | Finn | Alonso | Sylvain
6 (Discussion on how we are go-ing to design the robot) | Building a pro-totype version of the SMARS (with smaller competents that Tim has) | Modelling on Fusion 360, first model with diagonal stepped motors | Modelling on Fusion 360 and brainstorming | Modelling on Fusion360, second model with side by side stepped motors | Modelling and brainstorming on the software a connectivity through Wi-Fi
7 (Analysing SMARS pro-totype and 3D printed prototype chas-sis as well as clarifying the electric wiring) | Analyse 3D printed models, and draw an electric circuit | Compare and analyse 3D printed models | Learn how to control a stepped motor | Compare and analyse 3D printed models | Draw an elec-tric circuit to see if all connec-tions are good
Holidays (Start the soft-ware research, to learn how to correctly use our equipment and starting to understand how we are going to design and code the software) | Do research on ultrasonic sensor and how to use it and see how we can use python to utilize it’s data | Do research on stepper motor and how to use it and see how we can use python to utilize it’s data | Advance on the circuit and review prototype with the constraints of the wiring, if done check how to create a 2D map with Python | Advance on the circuit and review prototype with the constraints of the wiring, if done check how to create a 2D map with Python | Do research on IMU and how to use it, and see how we can use python to utilize it’s data
8 (Assemble the hardware, and the software) | Debugging the ultrasonic sensors code and real life testing | Playing around with the step-per motors and see how precious they are (code to real life ratio) | Debugging the ultrasonic sensors code and see how it would work with the 360 servo | Soldering and assembling the hardware | Soldering and assembling the hardware
9 (This should just be a debug-ging week and time to reflect a bit on how we are working as a team) | Debugging | Debugging (ca-ble management if necessary) | Debugging (hardware if cables fall off) | Debugging (re-modelling if nec-essary) | Debugging (re-modelling if nec-essary)

For now, we only planned individual tasks till week 9 (for Milestone) to see the dynamic of our group. When the first milestone is achieved, we will plan new weekly tasks for the next milestone.

7

## 0.8 Progress documentation

In development from Week 7 onwards...

We started to develop the chassis for the robot. First we need consider what it needs to hold, followed by how to arrange it. The robot will hold the 2 stepper motors, a servo, a battery and a micro-controller. For a first prototype, the stepper motors both go in the back, to compensate for the back weight, we would put the batteries and micro-controller in the front, finally in the center the servo holding the sensors.

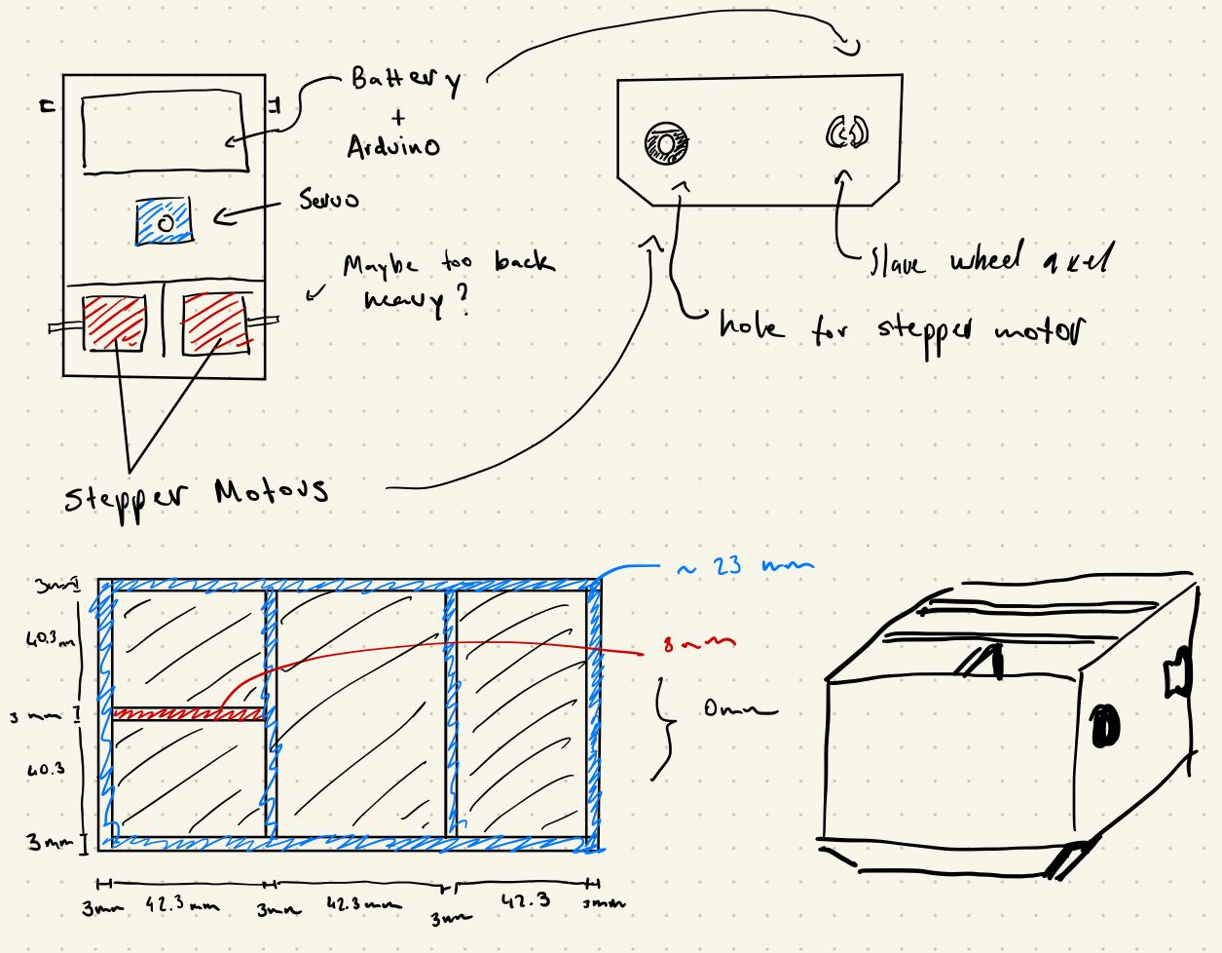
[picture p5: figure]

Our second prototype has the stepper motors diagonally spilt from each other. This version is more campact (smaller in terms of width). We want to test different configurations in turns of weight dispersion:

8

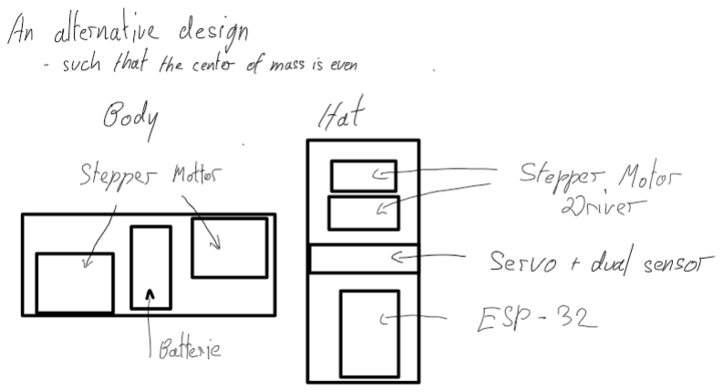
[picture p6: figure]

Here is first SMARS prototype with our own equipment. This will allow us to quickly test if tracks are a good use in our project, so we can change our design if this isn’t the case.

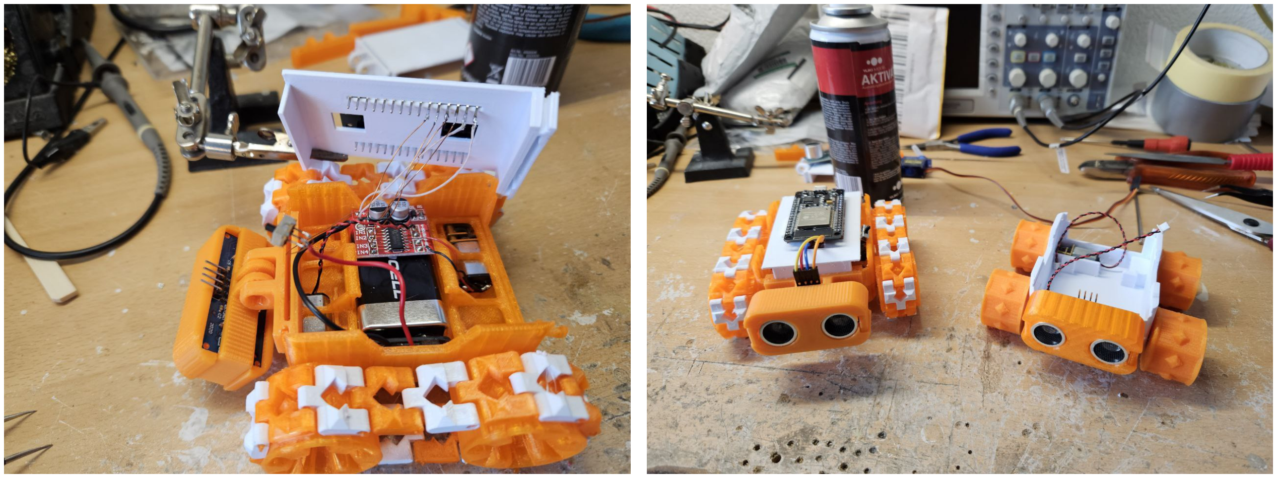
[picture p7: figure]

9

## 0.9 References

[1] Figure 1 : Alain Godot. Algorithmes SLAM (Simultaneous Localization and Mapping). May 2019. URL: https://www.innowtech.com/2019/05/16/les-algorithmes-slam-simultaneous-localization-and-mapping/ (https://www.innowtech.com/2019/05/16/les-algorithmes-slam-simultaneous-localization-and-mapping/)
[2] Figure 2 : @CodersCafeTech. DIY Radar With Ultrasonic Sensor And Chat-GPT Generated Arduino Code — Coders Cafe. Youtube. 2023. URL: https://youtube.com/shorts/o7DMHJKhpws?feature=share (https://youtube.com/shorts/o7DMHJKhpws?feature=share)
[3] Figure 3 : Channel Everything. Two ultrasonic sensors on a servo for angle and distance data. Youtube. 2016. URL: https://www.youtube.com/watch?v=dHZB0WhLl8g&t=12s
[4] Figure 4 : Hani’s Experiments. How to make an ultrasonic Radar. Youtube. 2021. URL: https://www.youtube.com/watch?v=xngpwyQKnRw
[5] Figure 5 : Kevin McAleer. SMARS Fan. 2018. URL: https://www.smarsfan.com

10

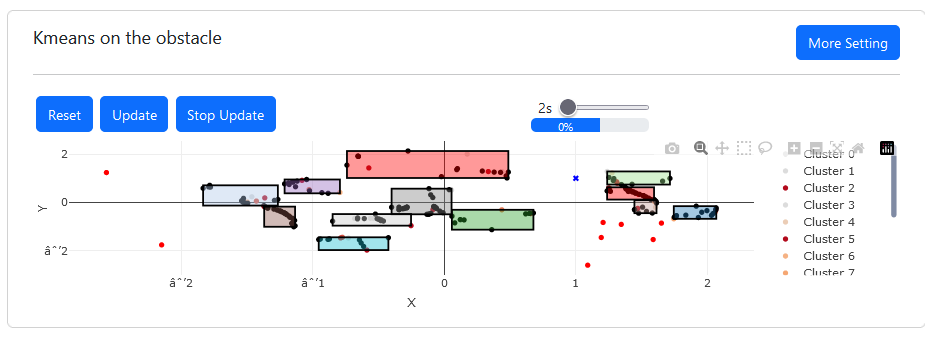
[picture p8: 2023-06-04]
Pictures/kmean.png

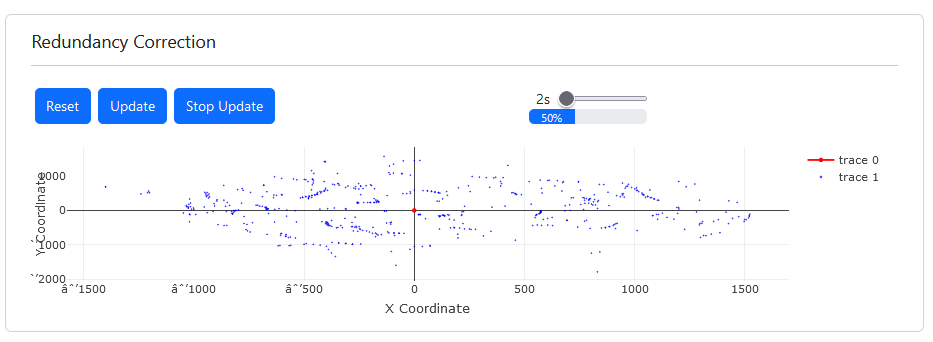
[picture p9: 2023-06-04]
Pictures/redundancy.png

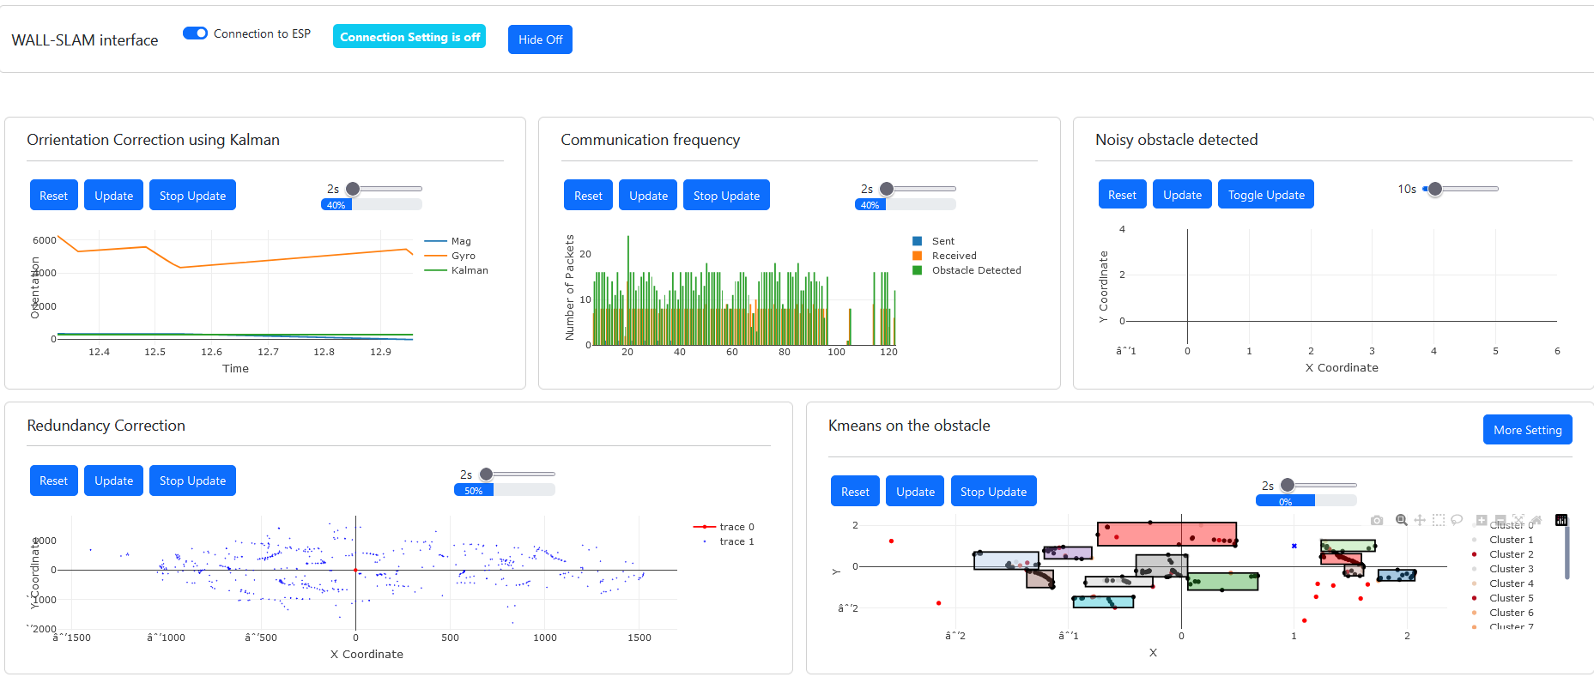
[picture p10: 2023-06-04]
Pictures/interface.png

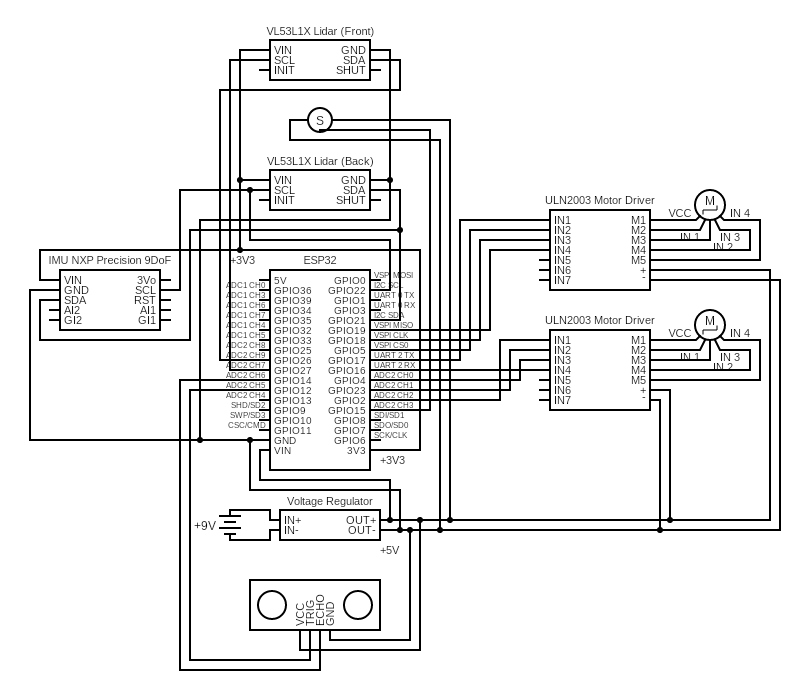
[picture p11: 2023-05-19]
circuit/circuit.png

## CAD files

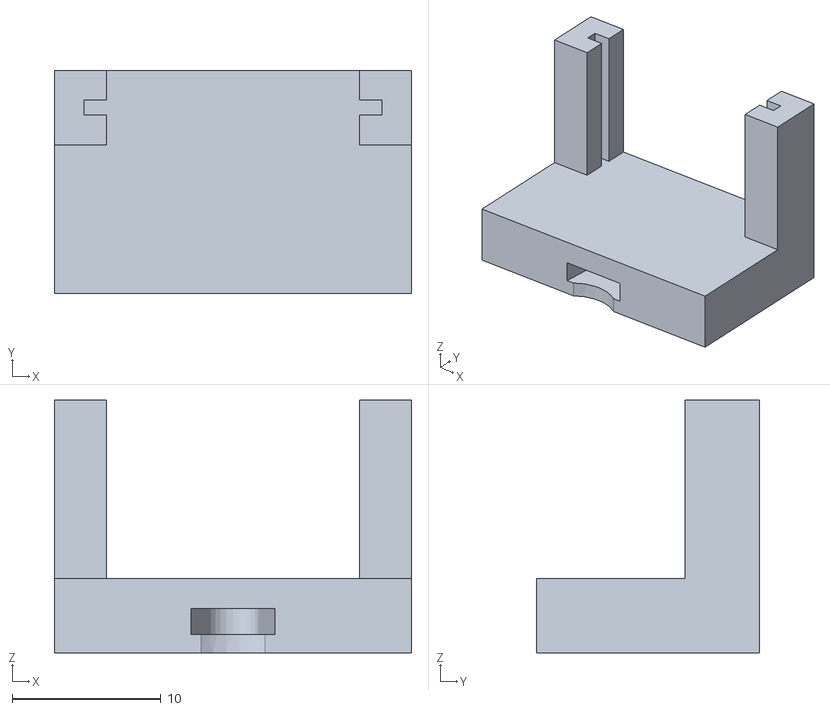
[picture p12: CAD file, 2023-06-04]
3DModels/lidarHolder.stl
24.0 x 15.0 x 17.0

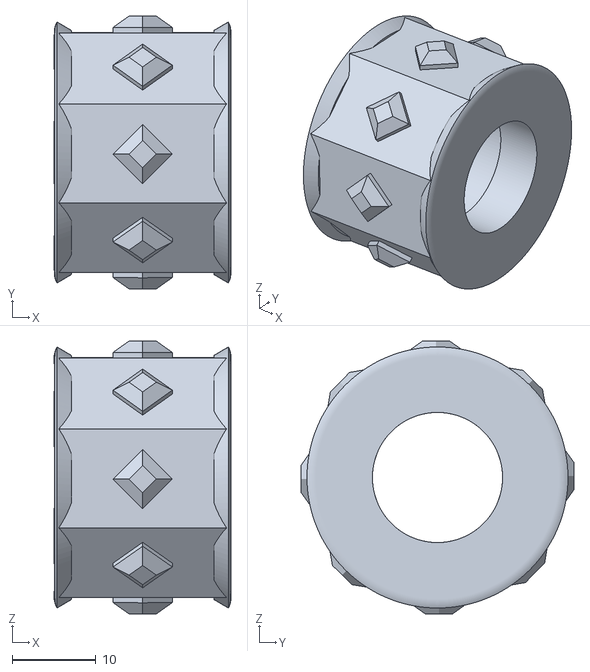
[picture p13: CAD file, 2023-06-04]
3DModels/slave_wheel_SL.stl
21.0 x 32.5 x 32.5

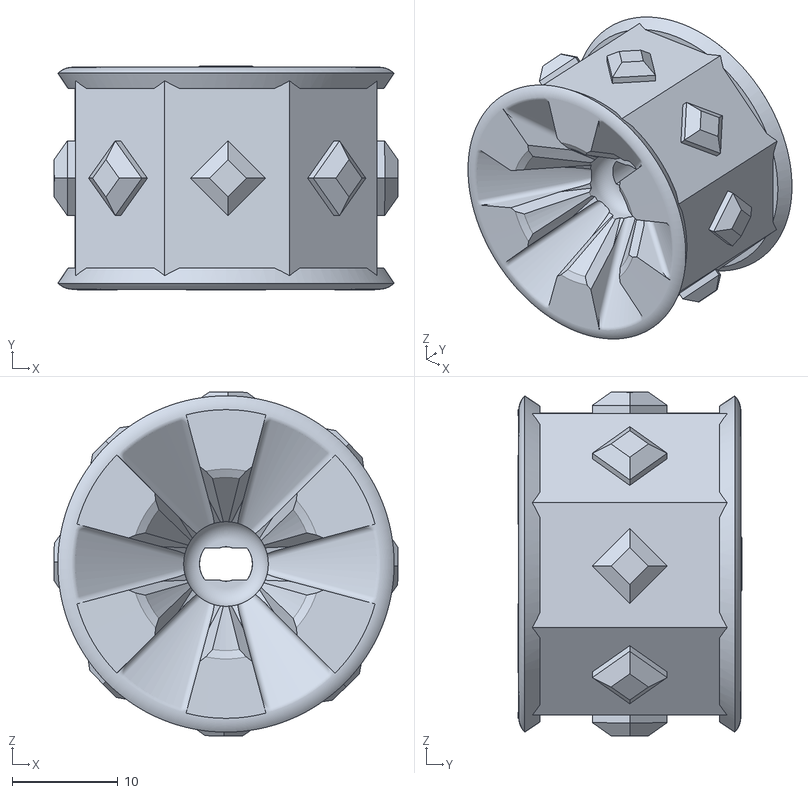
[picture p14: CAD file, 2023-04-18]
3DModels/motorWheel.stl
32.5 x 21.1 x 32.5

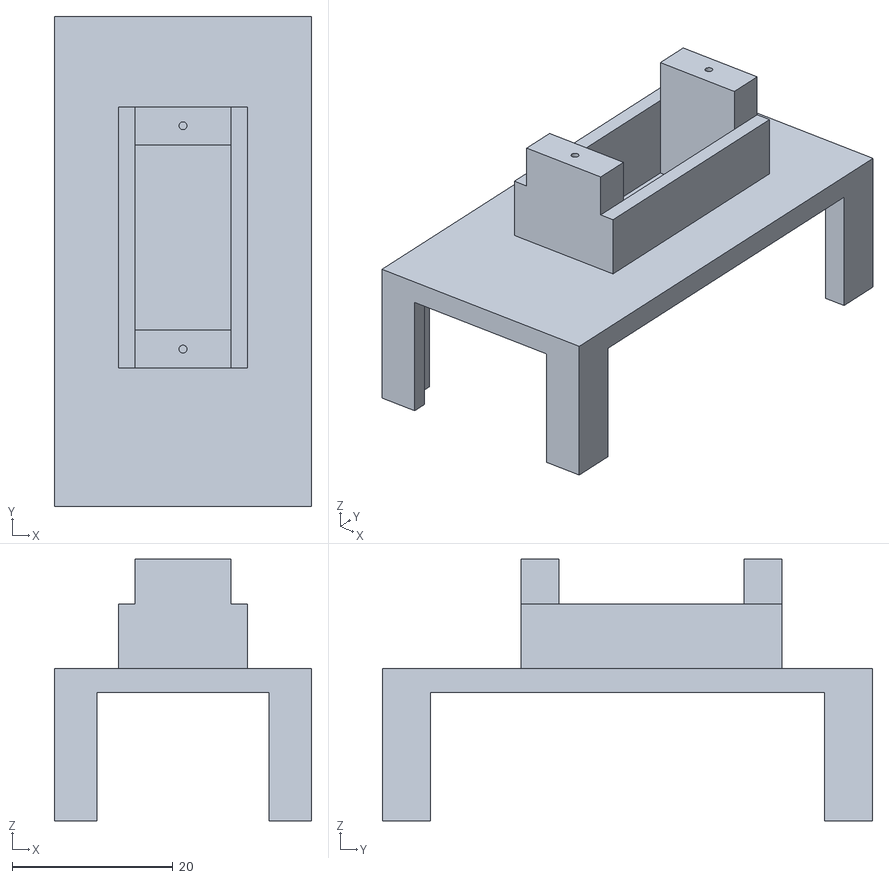
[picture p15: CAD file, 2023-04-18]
3DModels/servoHolder.stl
32.0 x 61.0 x 32.6

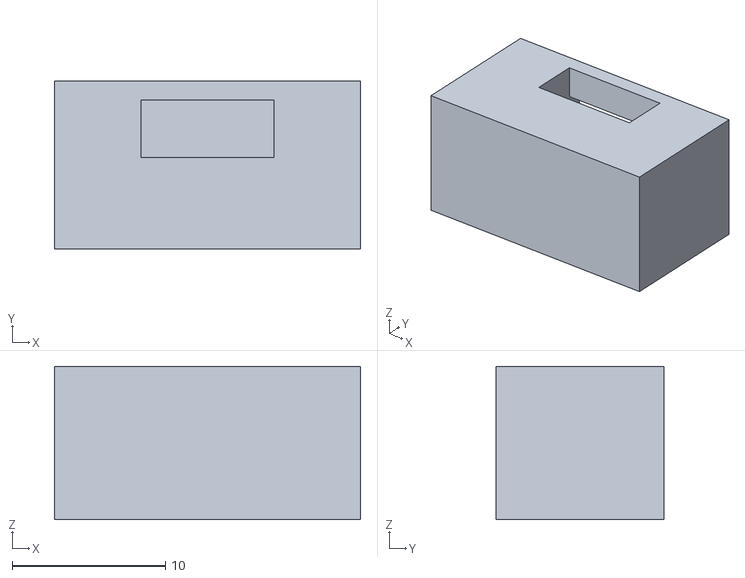
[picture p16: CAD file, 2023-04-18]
3DModels/interruptorHolder.stl
20.0 x 11.0 x 10.0

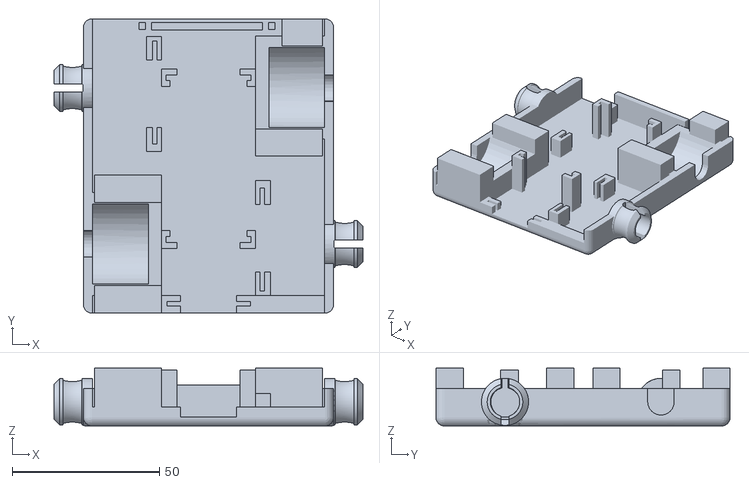
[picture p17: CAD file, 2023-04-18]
3DModels/chassisFilleted.stl
105.0 x 100.0 x 19.7

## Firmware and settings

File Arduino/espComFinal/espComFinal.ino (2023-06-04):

#include <WiFi.h>
#include <WebServer.h>
#include <NewPing.h>
#include <ESP32Servo.h>
#include "Adafruit_VL53L1X.h"
#include <Adafruit_FXAS21002C.h>
#include <Adafruit_FXOS8700.h>
#include <Adafruit_Sensor.h>
#include <Adafruit_Sensor_Calibration.h>
#include <Adafruit_AHRS.h>
#include <Wire.h>
#include <AccelStepper.h>
#include <WiFiUdp.h>
#include <math.h>
// Create instance of IMU Sensor and declare pointers to Adafruit sensor objects
Adafruit_Sensor *accelerometer, *gyroscope, *magnetometer;
#include "NXP_FXOS_FXAS.h"  // NXP 9-DoF breakout

// Task handle for managing the task 
TaskHandle_t Task1;

// Sensor event and control variables
sensors_event_t event;
sensors_event_t aevent, mevent;
float heading;
float prevHeading;
const int THRESHOLD_VALUE = 1;
const int SPEED_INCREMENT = 100;
float yaw;
float initialMagHeading = 0;

float gyroZ;
float orientationMag = 0;
// Define complementary filter variables
unsigned long prevTimestamp = 0;

int distanceSonarFront = 0;
int16_t lidarDistanceFront;
int16_t lidarDistanceBack;
float dataSend[12];
int servoAngle=1;
int numberOfConnectionOld = 0;
float actionNumber = 0;
int goToOrientation = 0;
float curr_x = 0;
float curr_y = 0;
unsigned long startTime; // Variable to store the start time
unsigned long elapsedTime;
uint32_t timestamp;
int direction = 1;

// Stepper motor and distance settings
const float ACCELERATION_STEPPER = 250.0;
const float MAX_SPEED_STEPPER = 2000;
const float CONST_SPEED_STEPPER = 500;
const int STEPS_PER_REV = 2038;
const int STEPS_90_DEG = 1680;
const int16_t MIN_LIDAR_DISTANCE = 150;  // in mm
const int16_t MIN_SONAR_DISTANCE = 40;  // in mm (in cm but we x10 the distance)
const int SERVO_INIT_POS = 84;
const int MAX_DISTANCE_SONAR = 400;
const float DIST_PER_STEP = 0.06;  // in mm per step

// Stepper motor stepping modes
#define FULLSTEP 4
#define HALFSTEP 8

// Ultrasonic sensor pins
#define TRIG_PIN 12
#define ECHO_PIN 14

// VL53L1X lidar sensor pins
#define IRQ_PIN 2
#define XSHUT_PIN 3

// Servo motor pin
#define servoPin 15

// I2C communication pins for Fronr lidar (the back one is set on standart I2C pins)
#define SDA_1 26
#define SCL_1 27

// Pins for left motor
#define L_IN1 2
#define L_IN2 23
#define L_IN3 4
#define L_IN4 16

// Pins for right motor
#define R_IN1 17
#define R_IN2 5
#define R_IN3 18
#define R_IN4 19

// IMU Settings
#if defined(ADAFRUIT_SENSOR_CALIBRATION_USE_EEPROM)
  Adafruit_Sensor_Calibration_EEPROM cal;
#else
  Adafruit_Sensor_Calibration_SDFat cal;
#endif

#define FILTER_UPDATE_RATE_HZ 100
#define PRINT_EVERY_N_UPDATES 10
//#define AHRS_DEBUG_OUTPUT

// Create instance of Servo
Servo servo;

// pick your filter! slower == better quality output
Adafruit_NXPSensorFusion filter; // slowest
//Adafruit_Madgwick filter;  // faster than NXP
//Adafruit_Mahony filter;  // fastest/smalleset

// Create instance of Lidar
Adafruit_VL53L1X vl53Front = Adafruit_VL53L1X(XSHUT_PIN, IRQ_PIN);
Adafruit_VL53L1X vl53Back = Adafruit_VL53L1X(XSHUT_PIN, IRQ_PIN);

// Create intance of Gyro, Accel and Mag
Adafruit_FXAS21002C gyro = Adafruit_FXAS21002C(0x0021002C);
Adafruit_FXOS8700 accelmag = Adafruit_FXOS8700(0x8700A, 0x8700B);

// Create instance of Ultrasonic sensor
NewPing frontUltrasonic(TRIG_PIN, ECHO_PIN, MAX_DISTANCE_SONAR);

// Create instances of stepper motors
AccelStepper stepperLeft(FULLSTEP, L_IN1, L_IN3, L_IN2, L_IN4);
AccelStepper stepperRight(FULLSTEP, R_IN1, R_IN3, R_IN2, R_IN4);

// SSID and password of Wifi connection:
const char* password = "0123456789A";
const char* ssid = "espWifi2";

// Port to send data
const uint16_t SEND_DATA_PORT = 8888;
const uint16_t RECIEVE_DATA_PORT = 8889;

bool isTurning = false;

//Open Wifi Port
WiFiServer sendServer(SEND_DATA_PORT);
WiFiServer recieveServer(RECIEVE_DATA_PORT);

// Initialize WiFi and WebServer objects
WiFiClient sendClient;
WiFiClient recieveClient;

// Configure IP addresses of the local access point
IPAddress local_IP(192, 168, 1, 22);
IPAddress user_IP(192, 168, 1, 23);

IPAddress gateway(192, 168, 1, 5);
IPAddress subnet(255, 255, 255, 0);

void setup() {
  Serial.begin(115200);



  // Servo Setup
  servo.attach(servoPin);
  servo.write(SERVO_INIT_POS);  // Put servo to initial position (looking forward)

  // Setup Front/Back lidars and IMU
  setupLidarsAndIMU();

  // Setup IMU Fusion algorithm
  setupIMUFusion();

  // Motors Setup
  stepperLeft.setMaxSpeed(MAX_SPEED_STEPPER);
  stepperLeft.setAcceleration(ACCELERATION_STEPPER);
  stepperRight.setMaxSpeed(MAX_SPEED_STEPPER);
  stepperRight.setAcceleration(ACCELERATION_STEPPER);
  // Access Point SetUp
  WiFi.softAPConfig(local_IP, gateway, subnet);
  WiFi.softAP(ssid, password);
  Serial.print("IP address = ");
  Serial.println(WiFi.softAPIP());

  // WifiServer Setup
  sendServer.begin();
  Serial.print("Sending Port is open at : ");
  Serial.println(SEND_DATA_PORT);

  recieveServer.begin();
  Serial.print("Recieving Port is open at : ");
  Serial.println(RECIEVE_DATA_PORT);


  // Setup core to Move
  xTaskCreatePinnedToCore(
    Task1code, /* Task function. */
    "Task1",   /* name of task. */
    10000,     /* Stack size of task */
    NULL,      /* parameter of the task */
    1,         /* priority of the task */
    &Task1,    /* Task handle to keep track of created task */
    1);        /* pin task to core 0 */
  delay(500);

  // Setup Timer
  startTime = millis(); // Record the start time
}

// Initializes lidar sensors and IMU.
void setupLidarsAndIMU() {
  while (!Serial) delay(10);

  Wire.begin();

  Wire1.begin(SDA_1,SCL_1);

  /* Initialise the sensor */
  if (!gyro.begin(0x21, &Wire)) {
    /* There was a problem detecting the FXAS21002C ... check your connections
     */
    Serial.println("Ooops, no FXAS21002C detected ... Check your wiring!");
    while (1)
      ;
  }
  if (!accelmag.begin(0x1F, &Wire)) {
    /* There was a problem detecting the FXOS8700 ... check your connections */
    Serial.println("Ooops, no FXOS8700 detected ... Check your wiring!");
    while (1)
      ;
  }

  if (! vl53Front.begin(0x29, &Wire1)) {
    Serial.print(F("Error on init of Front VL sensor: "));
    Serial.println(vl53Front.vl_status);
    while (1)       delay(10);
  }
  if (! vl53Back.begin(0x29, &Wire)) {
    Serial.print(F("Error on init of Back VL sensor: "));
    Serial.println(vl53Back.vl_status);
    while (1)       delay(10);
  }
  Serial.println(F("VL53L1X sensor OK!"));

  Serial.print(F("Sensor ID: 0x"));
  Serial.println(vl53Front.sensorID(), HEX);

  if (! vl53Front.startRanging()) {
    Serial.print(F("Front lidar Couldn't start ranging: "));
    Serial.println(vl53Front.vl_status);
    while (1)       delay(10);
  }
  if (! vl53Back.startRanging()) {
    Serial.print(F("Back lidar Couldn't start ranging: "));
    Serial.println(vl53Back.vl_status);
    while (1)       delay(10);
  }
  Serial.println(F("Ranging started"));

  // Valid timing budgets: 15, 20, 33, 50, 100, 200 and 500ms!
  vl53Front.setTimingBudget(50);
  Serial.print(F("Timing budget (ms): "));
  Serial.println(vl53Front.getTimingBudget());
}

// Initializes the IMU using Sensor Fusion Algorithm
void setupIMUFusion() {
  while (!Serial) yield();

  //if (!cal.begin()) {
  //  Serial.println("Failed to initialize calibration helper");
  //} else if (! cal.loadCalibration()) {
  //  Serial.println("No calibration loaded/found");
  //}

  if (!init_sensors()) {
    Serial.println("Failed to find sensors");
    while (1) delay(10);
  }

  setup_sensors();
  filter.begin(FILTER_UPDATE_RATE_HZ);
  timestamp = millis();

  Wire.setClock(400000); // 400KHz

  sensors_event_t mag;
  magnetometer->getEvent(&mag);
  // Calculate the initial magnetometer heading
  initialMagHeading = (180 * atan2(-mag.magnetic.y, mag.magnetic.x) / PI);
}

// Computes precise orientation using Fusion Sensor Algorithm, combining magnetometer and gyroscope data.
void getHeading() {
  
  float gx, gy, gz;
  static uint8_t counter = 0;

  if ((millis() - timestamp) < (1000 / FILTER_UPDATE_RATE_HZ)) {
    return;
  }
  timestamp = millis();
  // Read the motion sensors
  sensors_event_t accel, gyro, mag;
  accelerometer->getEvent(&accel);
  gyroscope->getEvent(&gyro);
  magnetometer->getEvent(&mag);
#if defined(AHRS_DEBUG_OUTPUT)
  Serial.print("I2C took "); Serial.print(millis()-timestamp); Serial.println(" ms");
#endif

  cal.calibrate(mag);
  cal.calibrate(accel);
  cal.calibrate(gyro);
  // Gyroscope needs to be converted from Rad/s to Degree/s
  // the rest are not unit-important
  gx = gyro.gyro.x * SENSORS_RADS_TO_DPS;
  gy = gyro.gyro.y * SENSORS_RADS_TO_DPS;
  gz = gyro.gyro.z * SENSORS_RADS_TO_DPS;

  gyroZ = gz;

  // Update the SensorFusion filter
  filter.update(gx, gy, gz, 
                accel.acceleration.x, accel.acceleration.y, accel.acceleration.z, 
                mag.magnetic.x, mag.magnetic.y, mag.magnetic.z);
#if defined(AHRS_DEBUG_OUTPUT)
  Serial.print("Update took "); Serial.print(millis()-timestamp); Serial.println(" ms");
#endif

  // only print the calculated output once in a while
  if (counter++ <= PRINT_EVERY_N_UPDATES) {
    return;
  }
  // reset the counter
  counter = 0;

#if defined(AHRS_DEBUG_OUTPUT)
  Serial.print("Raw: ");
  Serial.print(accel.acceleration.x, 4); Serial.print(", ");
  Serial.print(accel.acceleration.y, 4); Serial.print(", ");
  Serial.print(accel.acceleration.z, 4); Serial.print(", ");
  Serial.print(gx, 4); Serial.print(", ");
  Serial.print(gy, 4); Serial.print(", ");
  Serial.print(gz, 4); Serial.print(", ");
  Serial.print(mag.magnetic.x, 4); Serial.print(", ");
  Serial.print(mag.magnetic.y, 4); Serial.print(", ");
  Serial.print(mag.magnetic.z, 4); Serial.println("");
#endif

  // print the heading
  heading = filter.getYaw();
  //Serial.print("Orientation: ");
  //Serial.println(heading);
  
#if defined(AHRS_DEBUG_OUTPUT)
  Serial.print("Took "); Serial.print(millis()-timestamp); Serial.println(" ms");
#endif
}

// Reads distance from both lidars (front and back)
void readLidar() {
  if (vl53Front.dataReady()) {
    lidarDistanceFront = vl53Front.distance();
  } else {
    lidarDistanceFront = -1;
  }

  if (vl53Back.dataReady()) {
    lidarDistanceBack = vl53Back.distance();
  } else {
    lidarDistanceBack = -1;
  }
}

// Reads the data comming from the laptop side
void readData() {
  if (!recieveClient.connected()) {
    Serial.println("No client connected (Recieve)");
    recieveClient = recieveServer.available();
  } else {
    Serial.println("New client connected (Recieve)");
    if (recieveClient.connected() && recieveClient.available()) {
      // Read the packed dataRecieved from the socket
      float dataRecieved[1];
      recieveClient.read((byte*)dataRecieved, sizeof(dataRecieved));

      // Unpack the dataRecieved
      actionNumber = dataRecieved[0];

      // Do something with the decoded angles
      Serial.print("Action recieved: ");
      Serial.print(actionNumber);

      //action(actionNumber);
      // Send "200" back to the client
      recieveClient.write("200");
    }
  }
}

// Sends data to the laptop
void sendData() {
  packData();

  if (!sendClient.connected()){
    if(sendClient.connect(user_IP, SEND_DATA_PORT)) {
      Serial.println("Connected to server");
    } else{
      Serial.println("Non connection");
    }
  } else {
    sendClient.flush();
    sendClient.write((byte*)dataSend, sizeof(dataSend));
    Serial.println("Data Sent");
  }
}

//  Updates the distance and motion sensors (IMU, and both lidars on servo)
void updateSensors() {

  //Update Timer
  elapsedTime = (float)(millis() - startTime);

  // Ultrasonic Update
  distanceSonarFront = frontUltrasonic.ping_cm() * 10; 

  // Lidar Update
  rotateServo();
  readLidar();

  getHeading();

  // IMU Update
  gyro.getEvent(&event);
  accelmag.getEvent(&aevent, &mevent);

  // Orientation Update
  orientationMag = atan2(-mevent.magnetic.y, mevent.magnetic.x) * 180 / PI - initialMagHeading;

  if (orientationMag < 0) {
      orientationMag += 360;
    } else if (orientationMag >= 360) {
      orientationMag -= 360;
    }
  
  unsigned long currentTimestamp = millis();
  float deltaTime = (currentTimestamp - prevTimestamp) / 1000.0; // Convert milliseconds to seconds
  prevTimestamp = currentTimestamp;

  // Update the yaw
  yaw -= (gyroZ * 180/PI) * deltaTime;

   //Keep yaw within the range of 0 to 360 degrees
  if (yaw < 0) {
    yaw += 360;
  } else if (yaw >= 360) {
    yaw -= 360;
  }

  yaw = fmod(yaw, 360.0);
  
}

// Packs the data into packets for sending to laptop
void packData() {
  updateSensors();
  dataSend[0] = servo.read();
  dataSend[1] = distanceSonarFront;
  dataSend[2] = lidarDistanceFront;
  dataSend[3] = lidarDistanceBack;
  dataSend[4] = servo.read() + goToOrientation;
  dataSend[5] = curr_x;
  dataSend[6] = curr_y;
  dataSend[7] = elapsedTime;
  dataSend[8] = orientationMag; // Mag or
  dataSend[9] = yaw;  // Gyro Or
  dataSend[10] = heading;
  dataSend[11] = goToOrientation;
  //Serial.print("Orientation :");
  //Serial.print(goToOrientation);

  //Serial.println("magOrientation: "+ String(orientationMag));
  //Serial.println("gyroOrientation: "+ String(yaw));
  //Serial.println("Kalman heading: "+ String(heading));

}

// Sweeps the servo from 0 to 180 and backwards
void rotateServo() {
  if (servoAngle >= 180 || servoAngle <= 0) direction = -direction;
  servoAngle += direction;
  servo.write(servoAngle);

}

// Determines the behaviour of the car (moving, turning, stop)
void action(float actionNumber) {
  
  //Serial.println(distanceSonarFront);

  switch ((int)actionNumber) {
    case 0:
      stopMotors();
      break;
    case 1:
      if (distanceSonarFront <= MIN_SONAR_DISTANCE) {
        stopMotors();
      }
      else {
        moveForward();
      }
      
      break;

    case 2:
      moveBackward();
      break;

    case 3:
      moveRight();
      actionNumber = 0;
      break;

    case 4:
      moveLeft();
      actionNumber = 0;

      break;

    default:
      stepperLeft.run();
      stepperRight.run();
  }

  actionNumber = 0;
}


// Stops all motors
void stopMotors() {
  stepperLeft.setSpeed(0);
  stepperRight.setSpeed(0);
  stepperLeft.runSpeed();
  stepperRight.runSpeed();
}

// Moves the car forward
void moveForward() {
  stepperLeft.setSpeed(-CONST_SPEED_STEPPER);
  stepperRight.setSpeed(CONST_SPEED_STEPPER);
  if(stepperLeft.runSpeed()){
    if (goToOrientation == 0) {
        curr_y += DIST_PER_STEP;  // move north
    } else if (goToOrientation == 90) {
        curr_x += DIST_PER_STEP;  // move west
    } else if (goToOrientation == 180) {
        curr_y -= DIST_PER_STEP;  // move south
    } else if (goToOrientation == 270) {
        curr_x -= DIST_PER_STEP;  // move east
    }
  }
  stepperRight.runSpeed();
  
  correctHeading();
}

// Moves the car backward
void moveBackward() {
  stepperLeft.setSpeed(CONST_SPEED_STEPPER);
  stepperRight.setSpeed(-CONST_SPEED_STEPPER);
  if(stepperLeft.runSpeed()){
    if (goToOrientation == 0) {
        curr_y -= DIST_PER_STEP;  // move north
    } else if (goToOrientation == 90) {
        curr_x -= DIST_PER_STEP;  // move west
    } else if (goToOrientation == 180) {
        curr_y += DIST_PER_STEP;  // move south
    } else if (goToOrientation == 270) {
        curr_x += DIST_PER_STEP;  // move east
    }
  }
  stepperRight.runSpeed();
}

// Turns the car 90 degrees right
void moveRight() {
  goToOrientation = (int)(goToOrientation + 90) % 360;
  stepperLeft.setCurrentPosition(0);
  stepperRight.setCurrentPosition(0);
  stepperLeft.move(-STEPS_90_DEG);  // turn right 90 degrees
  stepperRight.move(-STEPS_90_DEG);
  while (stepperLeft.distanceToGo() != 0 || stepperRight.distanceToGo() != 0) {
    lidarDistanceFront = -1;
    lidarDistanceBack = -1;
    stepperLeft.run();
    stepperRight.run();
  }
  
}

// Turns the car 90 degrees left
void moveLeft() {
  goToOrientation = (int)(goToOrientation + 270) % 360;
  stepperLeft.setCurrentPosition(0);
  stepperRight.setCurrentPosition(0);
  stepperLeft.move(STEPS_90_DEG);  // turn right 90 degrees
  stepperRight.move(STEPS_90_DEG);
  while (stepperLeft.distanceToGo() != 0 || stepperRight.distanceToGo() != 0) {
    lidarDistanceFront = -1;
    lidarDistanceBack = -1;
    stepperLeft.run();
    stepperRight.run();
  }
}

// Corrects the orientation of the car while moving, using motion sensor and Kalman filter, to keep it moving in a straight line
void correctHeading() {
// Calculate the heading difference between the current and previous heading
float headingDiff = heading - prevHeading;

// Check if the heading difference exceeds a threshold value
if (abs(headingDiff) > THRESHOLD_VALUE) {
  // Adjust the speed of the motors
  if (headingDiff < 0) {
    // Increase the speed of the motors in the defeating direction
    stepperRight.setSpeed(CONST_SPEED_STEPPER - SPEED_INCREMENT);
    stepperLeft.setSpeed(-CONST_SPEED_STEPPER - SPEED_INCREMENT);
    stepperRight.runSpeed();
    stepperLeft.runSpeed();
    //Serial.println("INCREMENT LEFT");
  } else {
    // Decrease the speed of the motors in the defeating direction
    stepperRight.setSpeed(CONST_SPEED_STEPPER + SPEED_INCREMENT);
    stepperLeft.setSpeed(-CONST_SPEED_STEPPER + SPEED_INCREMENT);
    stepperRight.runSpeed();
    stepperLeft.runSpeed();
    //Serial.println("INCREMENT RIGHT");
  }
} else {
  // Reset the speeds to the constant values
  stepperRight.setSpeed(CONST_SPEED_STEPPER);
  stepperLeft.setSpeed(-CONST_SPEED_STEPPER);
  stepperRight.runSpeed();
  stepperLeft.runSpeed();
  }
  // Store the current heading as the previous heading for the next iteration
  prevHeading = heading;
}

// 
void Task1code(void* pvParameters) {
  for (;;) {
    action(actionNumber);
  }
}

// main loop code sending and receiving data fro
void loop() {
  if(WiFi.softAPgetStationNum() == 1){
    sendData();
    readData();
    delay(10);
  } 
}

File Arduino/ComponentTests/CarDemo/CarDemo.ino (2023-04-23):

#include <AccelStepper.h>
#include <NewPing.h>
#include <ESP32Servo.h>
#include "Adafruit_VL53L1X.h"
#include <Adafruit_FXAS21002C.h>
#include <Adafruit_FXOS8700.h>
#include <Adafruit_Sensor.h>
#include <Wire.h>

// Gyro Accel Mag (GAM)
#define SDA_2 26                                            // New I2C Data Pin
#define SCL_2 27                                            // New I2C Clock Pin
Adafruit_FXAS21002C gyro = Adafruit_FXAS21002C(0x0021002C); /* Assign a unique ID to the sensors at the same time */
Adafruit_FXOS8700 accelmag = Adafruit_FXOS8700(0x8700A, 0x8700B);

// VL53L1X Lidar
#define IRQ_PIN 2
#define XSHUT_PIN 3
Adafruit_VL53L1X vl53 = Adafruit_VL53L1X(XSHUT_PIN, IRQ_PIN);
const int16_t minLidarDistance = 150;  // in mm

// Sonar
#define trigPin 12
#define echoPin 14
const int maxSonarDistance = 400;  // in cm
const int minSonarDistance = 8;    // in cm
NewPing sonar(trigPin, echoPin, maxSonarDistance);

// Servo
#define servoPin 15
Servo servo;
const int servoInitPos = 84;  // 86 degrees
int servoAngle = servoInitPos;
int direction = 1;

// Left Motor
#define lIN1 2
#define lIN2 0
#define lIN3 4
#define lIN4 16

// Right Motor
#define rIN1 17
#define rIN2 5
#define rIN3 18
#define rIN4 19

// Define step constants
#define FULLSTEP 4
#define HALFSTEP 8

// Define acceleration and maximum speed values
const float acceleration = 250.0;
const float maxSpeed = 2000;
const float constSpeed = 1000;
const int STEPS_PER_REV = 2038;
const int STEPS_90_DEG = 1740;

// Creates two instances
// Pins entered in sequence IN1-IN3-IN2-IN4 for proper step sequence
AccelStepper stepperLeft(FULLSTEP, lIN1, lIN3, lIN2, lIN4);
AccelStepper stepperRight(FULLSTEP, rIN1, rIN3, rIN2, rIN4);

int sonarDistance;
int16_t lidarDistance;

const unsigned long interval = 10;
unsigned long previousMillis = 0;

void setup() {

  // Serial Monitor
  Serial.begin(115200);

  // Gyro Accel Mag (GAM)
  setupGAM();

  // Lidar
  setupLidar();

  // Servo
  servo.attach(servoPin);
  servo.write(servoInitPos);  // Put servo to initial position (looking forward)

  // Set initial speed and acceleration
  stepperLeft.setMaxSpeed(maxSpeed);
  stepperLeft.setAcceleration(acceleration);
  stepperRight.setMaxSpeed(maxSpeed);
  stepperRight.setAcceleration(acceleration);
}

void loop() {
  unsigned long currentMillis = millis();  // millis() = number of milliseconds that have elapsed since the board started running

  // Read lidar sensor
  readAndPrintLidar();
  // Print Gyro Accel Mag data
  //getEventGAM();

  // Read sonar sensor
  //sonarDistance = sonar.ping_cm();

  // If sonarDistance / lidarDistance is less than minDistance, turn right
  if (lidarDistance < minLidarDistance && lidarDistance != 0 && lidarDistance != -1) {
    stepperLeft.setCurrentPosition(0);
    stepperRight.setCurrentPosition(0);
    //delay(500);  // stop for 0.5 seconds
    stepperLeft.move(-STEPS_90_DEG);  // turn right 90 degrees
    stepperRight.move(-STEPS_90_DEG);
    while (stepperLeft.distanceToGo() != 0 || stepperRight.distanceToGo() != 0) {
      stepperLeft.run();
      stepperRight.run();
    }
  }

  moveForward();

  // This code executes every 10 milliseconds (rotating servo)
  if (currentMillis - previousMillis >= interval) {
    previousMillis = currentMillis;
    rotateServo();
  }
}

void moveForward() {
  // Move forward at constant speed if distance is greater than or equal to minDistance
  stepperLeft.setSpeed(-constSpeed);  // negative speed for left motor
  stepperRight.setSpeed(constSpeed);  // positive speed for right motor
  stepperLeft.runSpeed();
  stepperRight.runSpeed();
}

void rotateServo() {
  servoAngle += direction;
  if (servoAngle > 135 || servoAngle < 45) {
    direction *= -1;
  }
  servo.write(servoAngle);
  //Serial.println(servoAngle);
  //delay(10);
}

void printSonar() {
  Serial.print("Sonar distance: ");
  Serial.println(sonarDistance);
}

void readAndPrintLidar() {

  if (vl53.dataReady()) {
    // new measurement for the taking!
    lidarDistance = vl53.distance();
    if (lidarDistance == -1) {
      // something went wrong!
      Serial.print(F("Couldn't get lidar distance: "));
      Serial.println(vl53.vl_status);
      return;
    }
    Serial.print(F("Lidar distance: "));
    Serial.print(lidarDistance);
    Serial.println(" mm");

    // data is read out, time for another reading!
    //vl53.clearInterrupt(); // provokes an unnecessary delay
  }
}

void getEventGAM() {
  /* Get a new sensor event */
  sensors_event_t event;
  sensors_event_t aevent, mevent;

  /* Get a new sensor event */
  gyro.getEvent(&event);
  accelmag.getEvent(&aevent, &mevent);

  /* Display the results (speed is measured in rad/s) */
  Serial.print("G ");
  Serial.print("X: ");
  Serial.print(event.gyro.x);
  Serial.print("  ");
  Serial.print("Y: ");
  Serial.print(event.gyro.y);
  Serial.print("  ");
  Serial.print("Z: ");
  Serial.print(event.gyro.z);
  Serial.print("  ");
  Serial.println("rad/s ");
  //delay(500);

  /* Display the accel results (acceleration is measured in m/s^2) */
  Serial.print("A ");
  Serial.print("X: ");
  Serial.print(aevent.acceleration.x, 4);
  Serial.print("  ");
  Serial.print("Y: ");
  Serial.print(aevent.acceleration.y, 4);
  Serial.print("  ");
  Serial.print("Z: ");
  Serial.print(aevent.acceleration.z, 4);
  Serial.print("  ");
  Serial.println("m/s^2");

  /* Display the mag results (mag data is in uTesla) */
  Serial.print("M ");
  Serial.print("X: ");
  Serial.print(mevent.magnetic.x, 1);
  Serial.print("  ");
  Serial.print("Y: ");
  Serial.print(mevent.magnetic.y, 1);
  Serial.print("  ");
  Serial.print("Z: ");
  Serial.print(mevent.magnetic.z, 1);
  Serial.print("  ");
  Serial.println("uT");

  //delay(500);
}

void setupLidar() {
  //Serial.begin(115200);
  while (!Serial) delay(10);

  Serial.println(F("Adafruit VL53L1X sensor demo"));

  Wire.begin();
  if (!vl53.begin(0x29, &Wire)) {
    Serial.print(F("Error on init of VL sensor: "));
    Serial.println(vl53.vl_status);
    while (1) delay(10);
  }
  Serial.println(F("VL53L1X sensor OK!"));

  Serial.print(F("Sensor ID: 0x"));
  Serial.println(vl53.sensorID(), HEX);

  if (!vl53.startRanging()) {
    Serial.print(F("Couldn't start ranging: "));
    Serial.println(vl53.vl_status);
    while (1) delay(10);
  }
  Serial.println(F("Ranging started"));

  // Valid timing budgets: 15, 20, 33, 50, 100, 200 and 500ms!
  vl53.setTimingBudget(50);
  Serial.print(F("Timing budget (ms): "));
  Serial.println(vl53.getTimingBudget());

  /*
  vl.VL53L1X_SetDistanceThreshold(100, 300, 3, 1);
  vl.VL53L1X_SetInterruptPolarity(0);
  */
}
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

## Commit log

2023-04-22 Car Demo (comment rotating servo)
2023-05-02 Update esp32Connection.py
    Works but when disconnected, can't reconnect probablely because of method _is_socket_alive_ or line 76 (waiting to recieve something but nothing comes)
2023-05-07 Update espComm.ino
    Useless print deleted
2023-05-09 Updated esp32Connection.py for movement
2023-05-11 added switch logic to web
2023-05-16 added Sensor Fusion using Kalman. Need testing.
2023-05-18 kalman filtering - needs variance for imu
2023-05-21 is working at this stage
2023-05-22 filter up
2023-05-23 working filter
2023-05-24 removed thread lock
2023-05-30 fixed movement button
2023-05-31 removed print
2023-06-01 remove print
